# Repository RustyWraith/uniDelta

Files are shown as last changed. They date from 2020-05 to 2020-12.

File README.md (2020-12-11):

# uniDelta
Parametric and scalable design of a delta 3d-printer frame.

# Preview
See on autodesk site.
https://a360.co/3fAnUOM

# Description
Key features, I made this design around:
+ be suitable for any size of a delta printer
+ use of aluminum extrusion and basic accessories
+ be suitable for V-slot sliders or linear rails
+ easy to enclose
+ be easily customizable for any size
+ cheap

Project is designed in Fusion 360.

# How to use this model
Use .f3z file to import it into Fusion 360.
Make sure "geometry_ref" sketch is visible. Make sure dimentions on the sketch are shown. If not, right click on sketch in browser -> Show Dimentions.
Then check model parameters in "Modify > Change Parameters" menu. Here you can find parameters, that make this design universal.
- *bed_diameter* -> Set it to a diameter of your working space. Usually, you want it to coincide with a dimeter of your printing bed.
- *bed_to_stand_offset* -> This is a distance from bed edge to a vertical stand. You should consider a number of factors, when assigning this parameter.
  - Size of your effector. There sould be enough offset to a nozzle to being able to reach a bed edge.
  - Mount points of printer arms on a slider carriage. Arms should not go any further than a vertical position, when a nozzle reaches an edge of working space.
  - Keep bed inside a frame perimeter, if you want to make a printer enclosed. If not, it is not crucial
- *height* -> Overall height of a frame.
- *T_stand* -> Vertical stands design is based on goeland86/MonsterKossel. So vertical stands are made of one 2040and one 2060 rods slaped together for super rigidity for bigger frames. If you want a small one or cut a budget, set *T_stand* to 0. Then make now unused 2060 invisible. Set *T_stand* to anything other than 1 or 0 to see various bugs.
Now about sad things. Fusion 360 is limited in a way how parameters are calculated. So, for now, you are not able to make a driven dimention on a scketch a paraeter. That leaves two options. Either I have to analitically solve all the geometry (and I do not have courage for that) or some parameters have to be manually transferred from *geometry_ref* sketch to a parameters menu. I choose a latter option. So, please, refer to *geometry_ref* sketch and enter following parameters.
- *side_extrusion* -> The length of side extrusions on bottom and top, that forms rings around vertical stands. Enter a corresponding number from *geometry_ref* sketch. If you do not cut extrusions yourself, usually it comes cut to a 1mm precision (like from soberyzavod.ru). So you want to adjust *bed_to_stand_offset* untill it yelds in a nice round side_extrusion length. It will help you to keep a geometry tight at an assembly process.
- *inner_extrusion* -> The lentght of inner pieces of extrusion. Enter a corresponding number from *geometry_ref* sketch.

# Options and modifications
- you can change *T_stand* parameter to use only 2040 extrusion as vertical stands
- ring of 2020 extrusions on the bottom are optional. If you will choose not use them I recommend to fasten 2040 ring with not one, but two L-brakets to each vertical stand
- I would recommend to use OpenBuilds type of L-brakets to fasten bottom ring to vertical stands (6 pcs.) because of their strict 10x10x10 dimensions and 90 deg. edges. It will keep geometry strict. However, you can get away with using any type of plates and brackets in other connections. Get cheap ones or 3d-print them.
- Archie delta robot compatible design. https://www.thingiverse.com/thing:3489886
- I advise to use v-slot for vertical 2040. Then it will be compatible with v-slot carriage in case of modification or selling.

*_If you don't have ability to use Fusion 360, please, feel free to request design needed via "Issues". I will try ti generate .step for you._*

# Bill of materials
## 300x800mm kossel delta frame
### Aluminum extrusion
- [2020](https://www.soberizavod.ru/catalog/seriya_20_obychnyy_paz/profil_konstruktsionnyy_20kh20l_bez_pokrytiya/)
  - 398mm **x6**
  - 168mm **x3**
  - 136mm **x1**
  - 134mm **x6**
- [2040](https://www.soberizavod.ru/catalog/seriya_20_obychnyy_paz/profil_konstruktsionnyy_20kh40l_bez_pokrytiya/)
  - 398mm **x3**
  - 168mm **x3**
  - 134mm **x3**
  - 800mm ([v-slot](https://www.soberizavod.ru/catalog/seriya_20_v_paz/profil_konstruktsionnyy_v20kh40l_bez_pokrytiya/)) x3
- [2060](https://www.soberizavod.ru/catalog/seriya_20_obychnyy_paz/profil_konstruktsionnyy_20kh60l_bez_pokrytiya/)
  - 800mm **x3**
- [Tools to control angles](https://aliexpress.ru/item/4000766779600.html)
### Plates and brackets
- [60 degree plate](https://www.soberizavod.ru/catalog/pod_uglom_seriya_20/u_soedinitel_60_gradusov_4_otv_paz_6_l57/) **x30**
- [Openbuilds L-type 3-slot](https://aliexpress.com/item/32843660148.html) **x6**
- [L-type bracket 3-slot](https://www.soberizavod.ru/catalog/uglovye_soediniteli_seriya_20/ugolok_20kh60l_paz_6_m52/) **x3**
- [L-type btacket 1-slot](https://www.soberizavod.ru/catalog/uglovye_soediniteli_seriya_20/ugolok_20kh20l_paz_6_m51/) **x12**
- [L-type plate](https://www.soberizavod.ru/catalog/g_obraznye_seriya_20/g_soedinitel_40kh60v_paz_6_l60/) **x2**
- [T-type plate](https://www.soberizavod.ru/catalog/t_obraznye_seriya_20/t_soedinitel_40kh50v_paz_6_l69/) **x1**
- [2-slot plate](https://www.soberizavod.ru/catalog/pryamougolnye_seriya_20/soedinitel_20kh40_paz_6_m45/) **x2**
- [motor plate](https://aliexpress.com/item/32813261164.html) **x3**
- [4040 plate (to move motors closer to stands)](https://www.soberizavod.ru/catalog/pryamougolnye_seriya_20/soedinitel_40kh40_paz_6_m48/) **x3**
### Kinematics
- [MGN12H with rail](https://aliexpress.com/item/32787326334) 500mm **x3**
- GT2 Gates timing belt **5 meters**
- GT2 Gates timing belt (for flying extruder lift, take cheapest)  **2 meters**
- M5x55 bolts (for top idlers) **x3**
- M5x30 bolts (for flying extruder lift) **x2**
- [Rubber band 4mm](https://aliexpress.com/item/32882540825.html) **4 meters**
- GT2 20t Pulley 5mm bore **x3**
- GT2 20t Idler Pulley 5mm bore **x3**
- Arms **x6**
  - [Magballs](https://duet3d.com/BallStudEnds) **x12**
  - Carbon fiber tubes, 318mm (5mm Inner Diameter) or (2mmID to use without M3 inserts, not recommended) **x12**
  - [Cup magnets B16](https://aliexpress.com/item/32966899291.html) **x12**
  - [M3 inserts (for 5mm ID carbon tube)](https://aliexpress.com/item/32811461060.html) **x12**
- Fastners
  - [M5x8](https://aliexpress.com/item/32811776016.html) **x300**
  - M5x12 **x6**
  - [M3 assorted](https://aliexpress.com/item/32831757502.html) **x1**
  - [M3x8](https://aliexpress.com/item/32769412937) **x30**
  - [M5 alum washers openbuilds 6.35mm](https://aliexpress.com/item/32753534988.html) **x18**
  - [M5 t-nuts](https://aliexpress.com/item/32706324351.html) **x300**
  - M3 t-nuts **x50**
  - M3 and M5 regular nuts and washers
  
# TODO
- Building instructions.

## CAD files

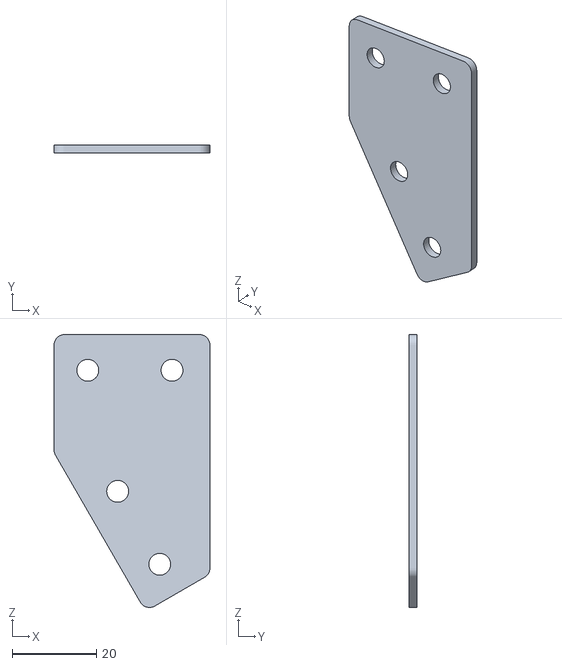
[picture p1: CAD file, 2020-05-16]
STLs/60deg_plate.stl
37.0 x 2.00 x 64.8

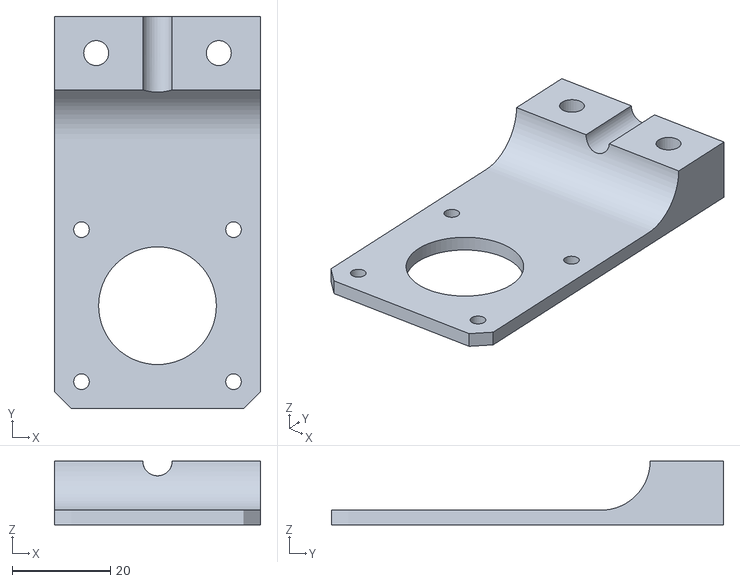
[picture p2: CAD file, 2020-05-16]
STLs/extruder+motor_plate.stl
42.0 x 80.0 x 13.0

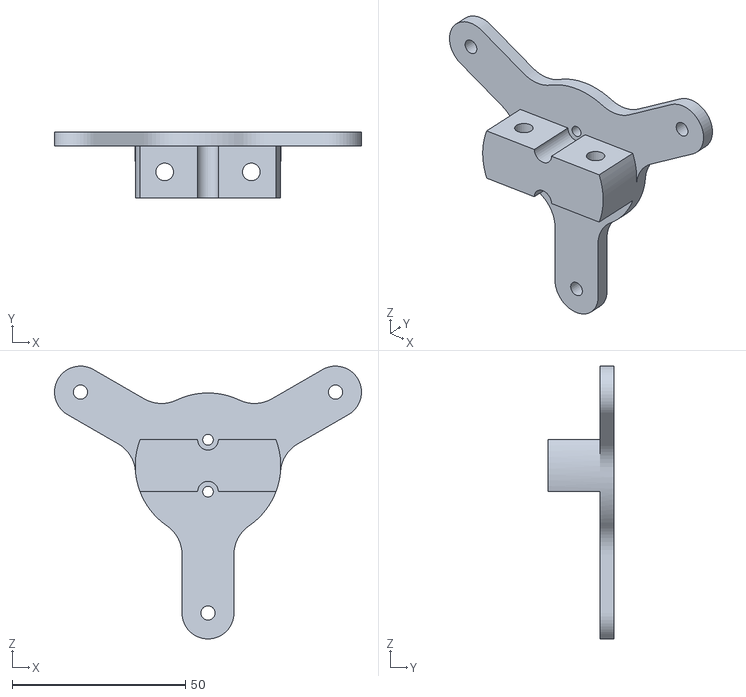
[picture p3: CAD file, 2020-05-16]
STLs/flying_extruder.stl
88.6 x 19.0 x 78.7

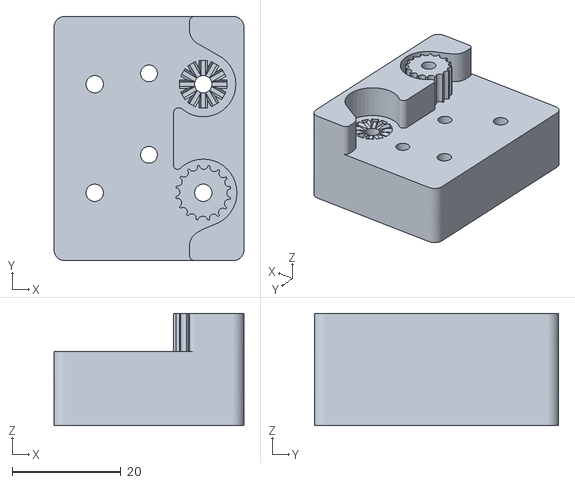
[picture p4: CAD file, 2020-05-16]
STLs/carriage.stl
35.0 x 45.0 x 20.7

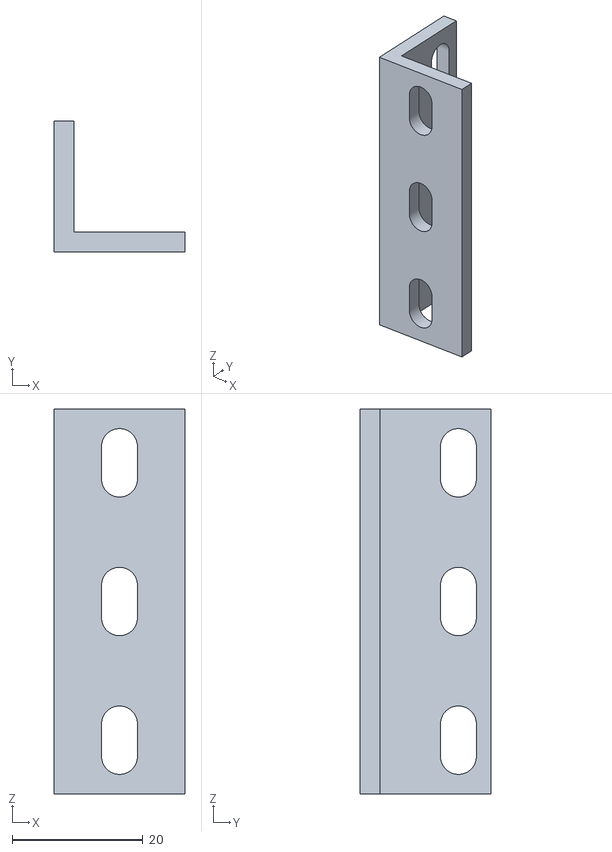
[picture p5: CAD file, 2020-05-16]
STLs/L-braket.stl
20.0 x 20.0 x 59.0

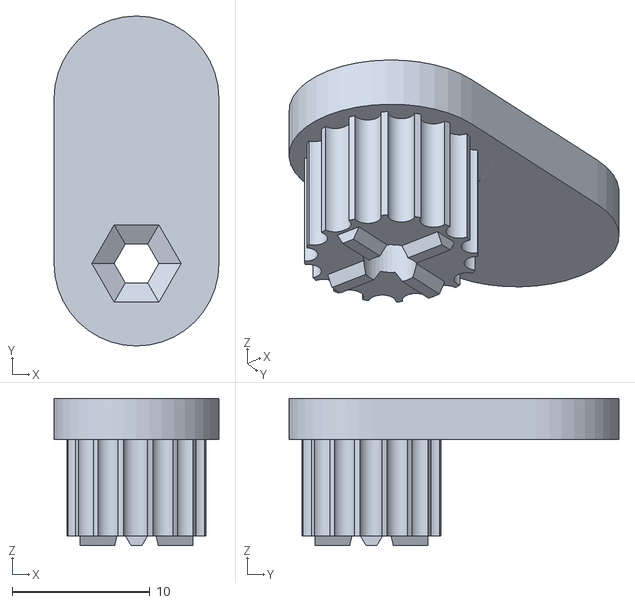
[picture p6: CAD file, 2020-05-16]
STLs/tensioner.stl
12.0 x 24.0 x 10.7

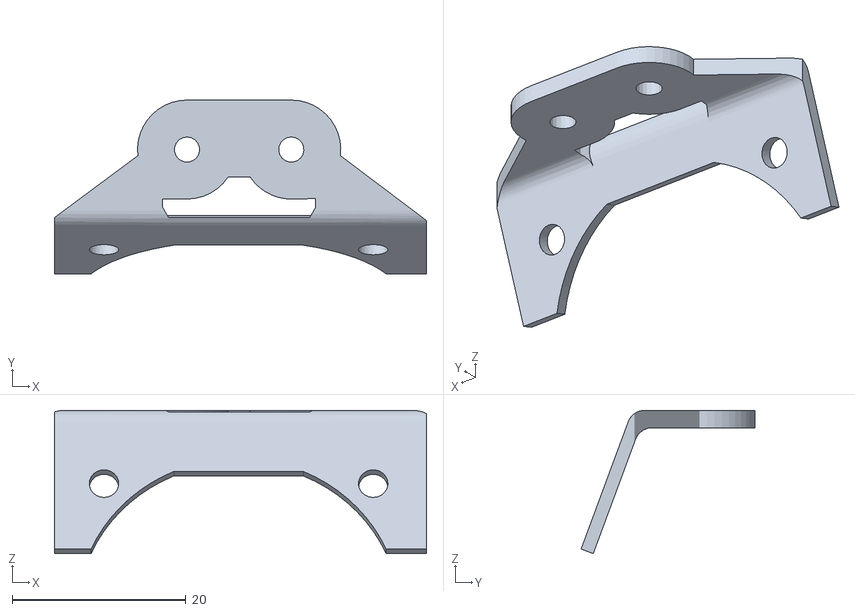
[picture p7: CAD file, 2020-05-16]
STLs/fan_mount.stl
42.8 x 20.0 x 16.5

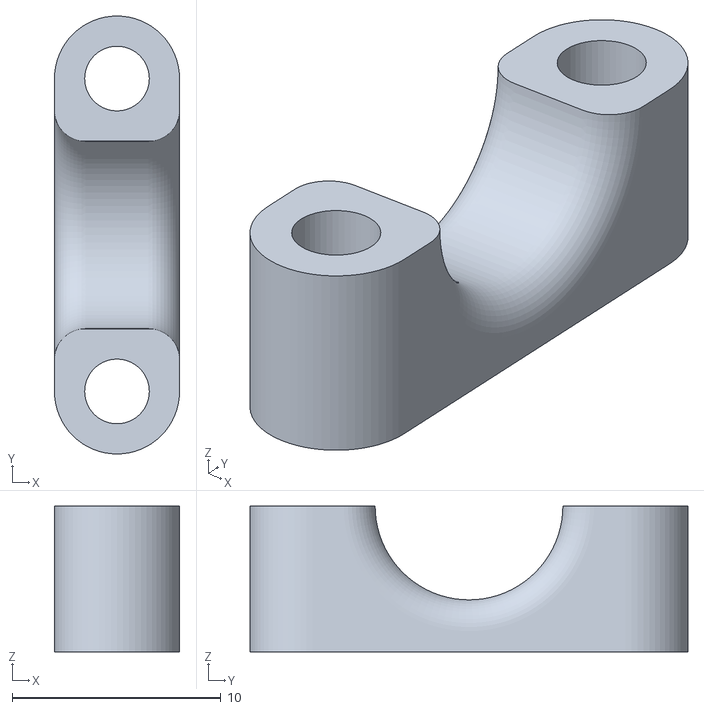
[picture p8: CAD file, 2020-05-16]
STLs/hook.stl
6.00 x 21.0 x 7.00

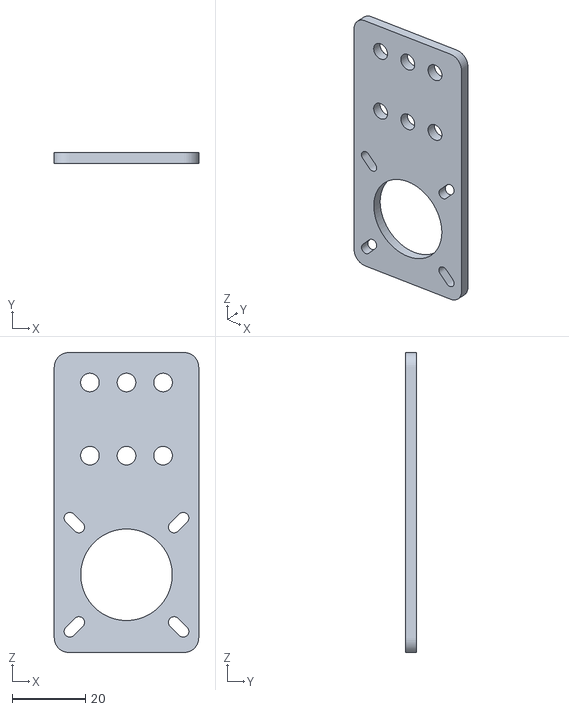
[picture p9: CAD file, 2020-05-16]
STLs/motor_plate.stl
39.5 x 3.00 x 82.0

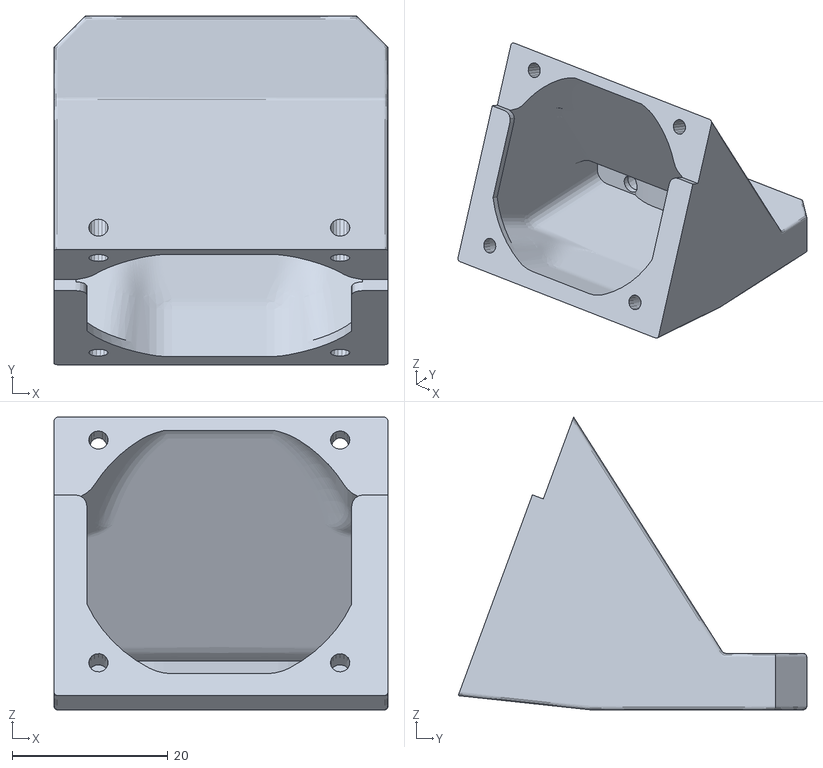
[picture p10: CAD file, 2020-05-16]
STLs/fanduct.stl
42.8 x 44.7 x 37.6

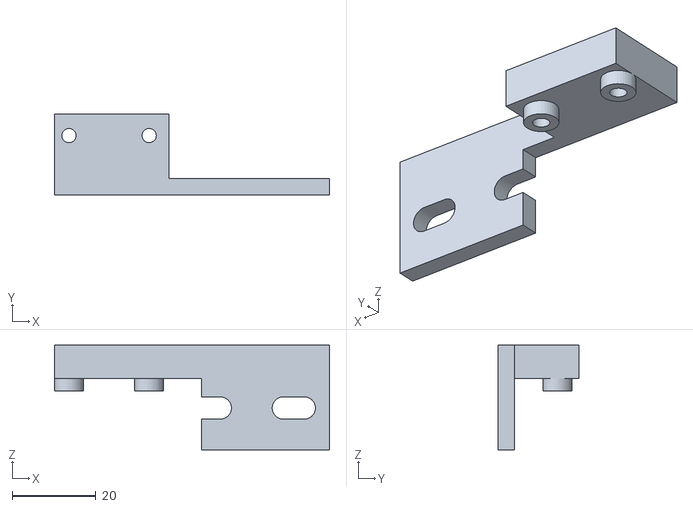
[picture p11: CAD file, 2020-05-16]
STLs/endstop.stl
65.5 x 19.4 x 25.0

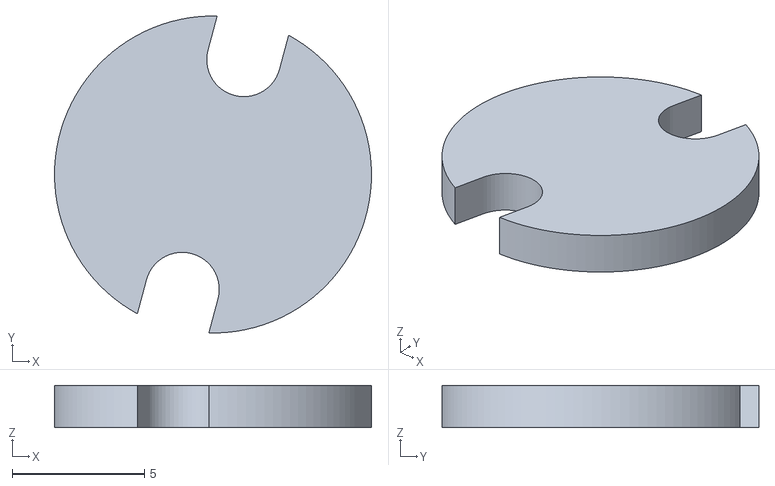
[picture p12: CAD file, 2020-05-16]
STLs/mosquito_washer.stl
12.0 x 12.0 x 1.60

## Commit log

2020-05-16 Initial set of STLs
    [60deg_plate.stl, L-braket.stl, carriage.stl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]
2020-05-16 BOM for 300x800 added
2020-12-11 BOM corection
2020-12-11 Corrected Arms BOM
